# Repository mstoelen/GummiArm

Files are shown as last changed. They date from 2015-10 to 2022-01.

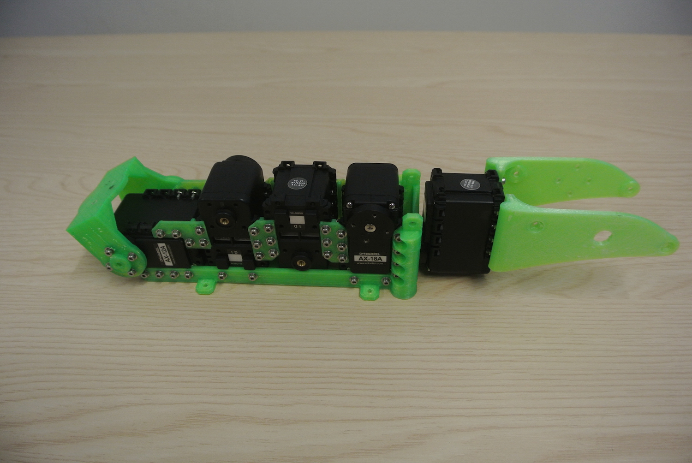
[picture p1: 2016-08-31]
media/instructions/media/building/lower_arm/fourth_step_2.JPG

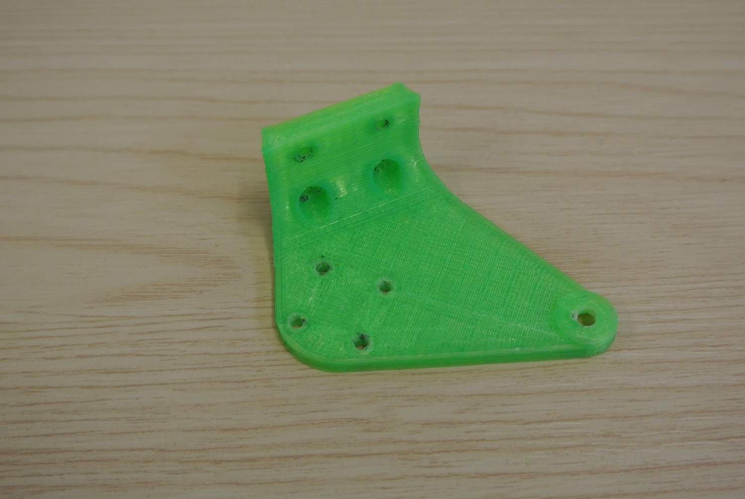
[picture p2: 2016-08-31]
media/instructions/media/plastic/upper_shoulder/left_clavicle.JPG

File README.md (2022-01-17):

# GummiArm

**Note:** This repository was archived on 24/04/2019. Last tested last on ROS Kinetic Kame. Checkout the new GummiArm Community Edition here: https://github.com/GummiArmCE

Repository for the GummiArm robot project: http://mstoelen.github.io/GummiArm/

Documentation in the wiki: https://github.com/mstoelen/GummiArm/wiki

Detailed build instructions <a href="http://htmlpreview.github.io/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">here</a>.

Videos: https://plus.google.com/collection/oGXbV

<br />This work is licensed under a <a rel="license" href="http://creativecommons.org/licenses/by-sa/4.0/">Creative Commons Attribution-ShareAlike 4.0 International License</a>.

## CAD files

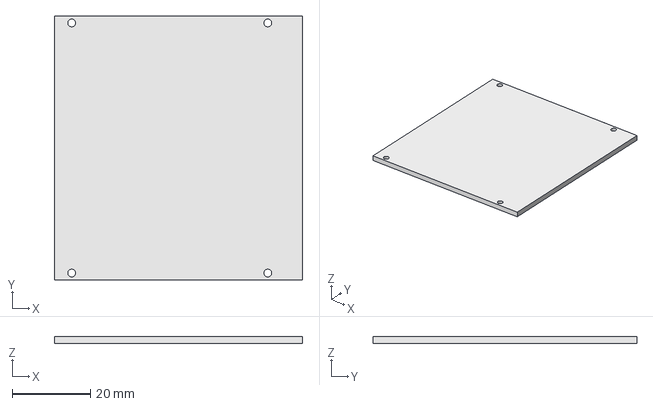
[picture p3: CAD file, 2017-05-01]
printables/accessories/smps_to_dyna_case_top.FCStd
63.6 x 67.6 x 1.86 mm

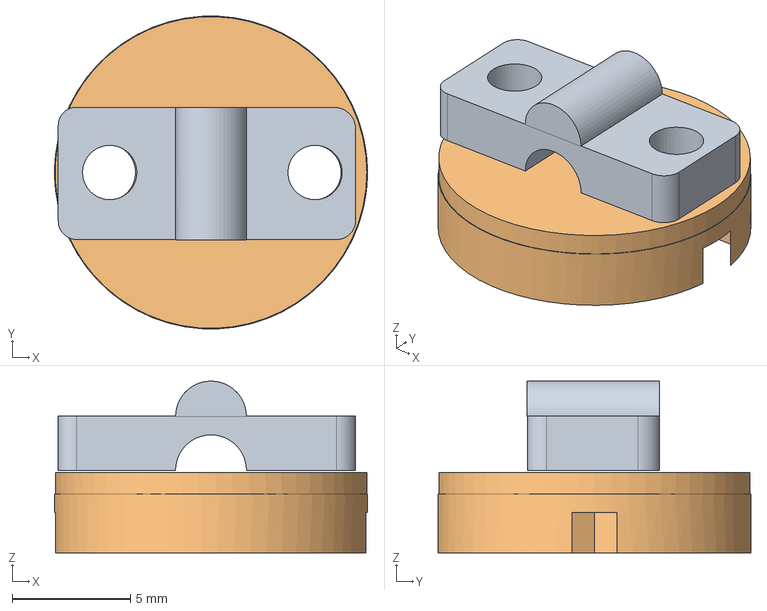
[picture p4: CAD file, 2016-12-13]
printables/common/tendon_joiner.FCStd
13.3 x 13.2 x 7.28 mm
top001

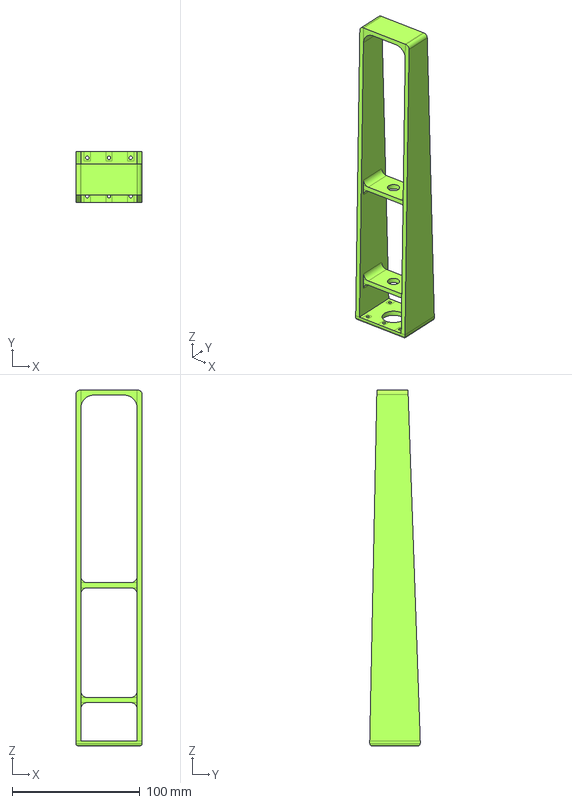
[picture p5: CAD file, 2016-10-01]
printables/dummies/upper_arm_dummy.FCStd
52.0 x 39.6 x 279.0 mm

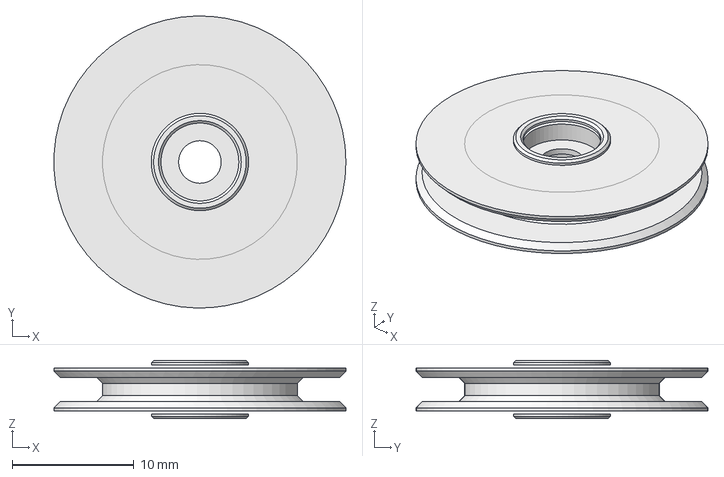
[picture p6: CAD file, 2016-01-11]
printables/hand/big_pulley_w_bearing.FCStd
24.0 x 24.0 x 4.80 mm

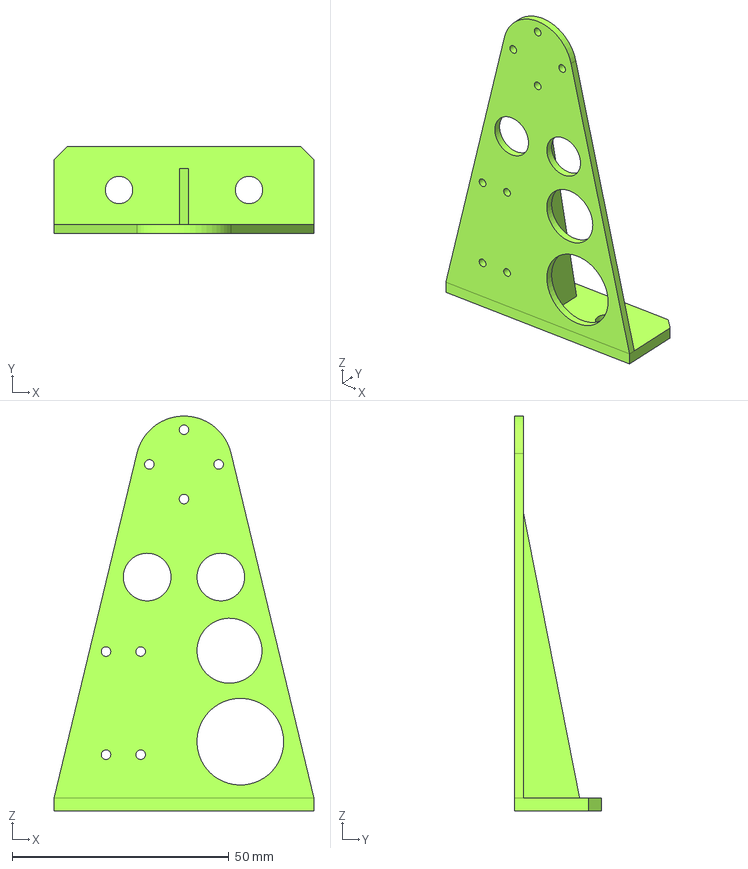
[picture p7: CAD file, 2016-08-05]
printables/head/encoder_frame.FCStd
60.0 x 20.0 x 91.2 mm

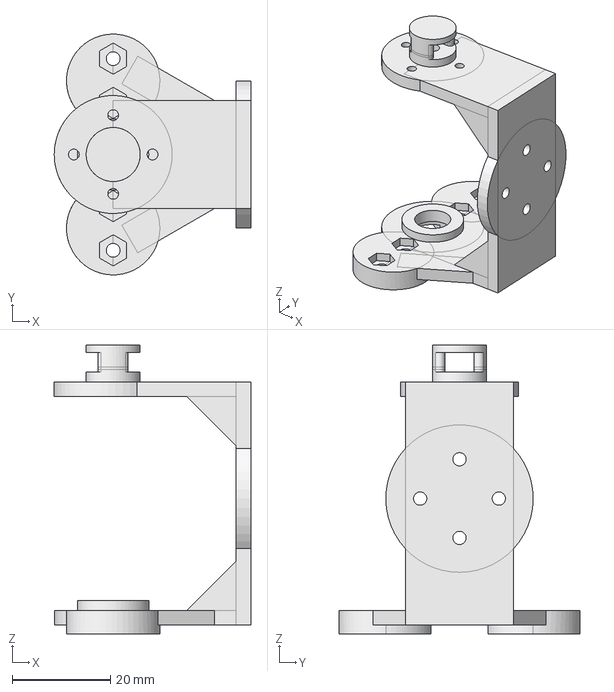
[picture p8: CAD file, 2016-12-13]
printables/lower_arm/wrist_frame.FCStd
40.0 x 49.0 x 58.8 mm

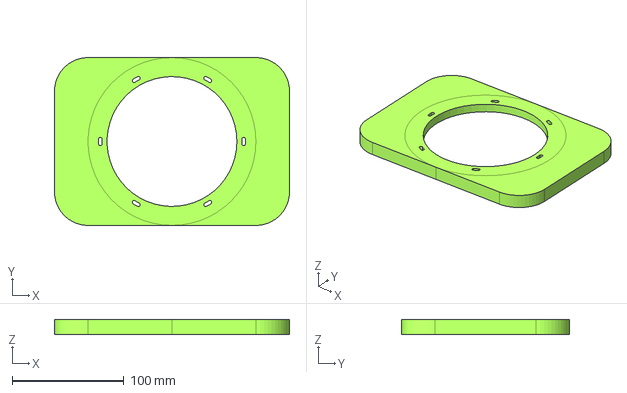
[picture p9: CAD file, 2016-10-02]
printables/mounts/table_flat_mount_bearing.FCStd
210.0 x 150.0 x 13.0 mm

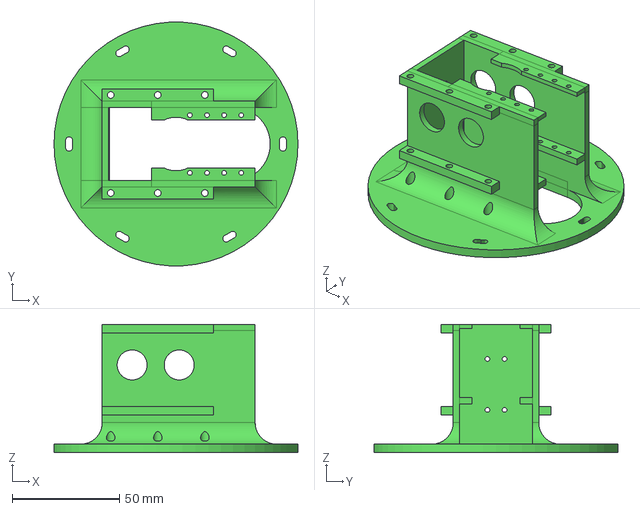
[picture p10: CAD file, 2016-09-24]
printables/shoulder/underside_plate.FCStd
114.0 x 113.8 x 60.0 mm

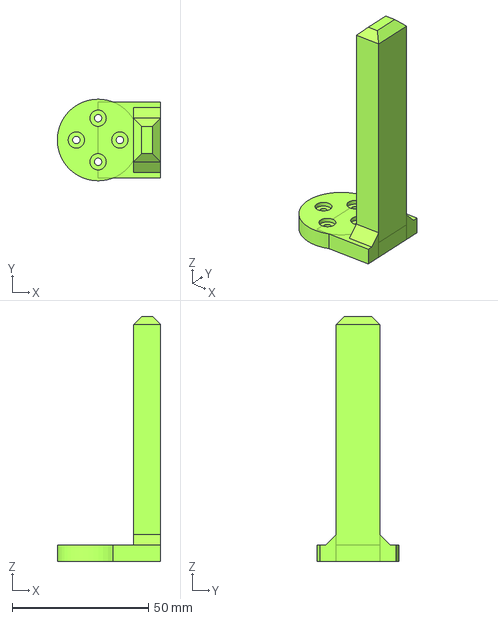
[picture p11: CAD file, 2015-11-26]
printables/tools/straight_finger.FCStd
38.0 x 30.0 x 90.0 mm

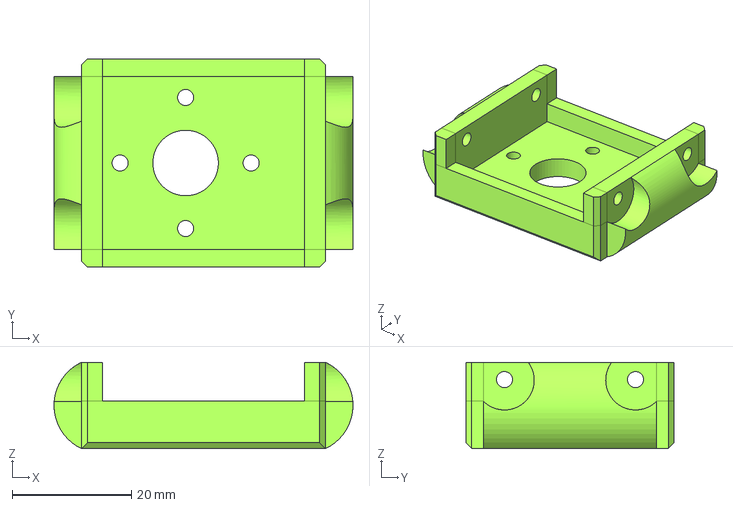
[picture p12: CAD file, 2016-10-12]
printables/upper_arm/top_mx-64_mount.FCStd
50.2 x 35.0 x 14.5 mm

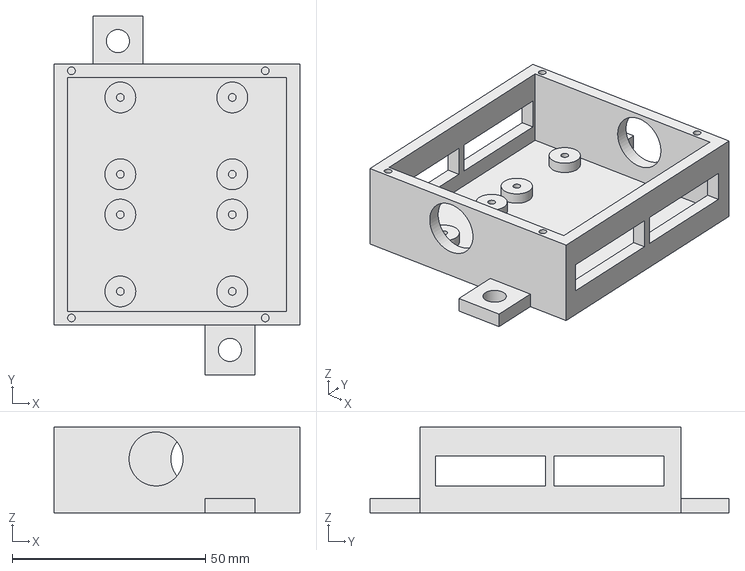
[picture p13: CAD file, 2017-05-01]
printables/accessories/smps_to_dyna_case.FCStd
63.6 x 93.0 x 22.3 mm

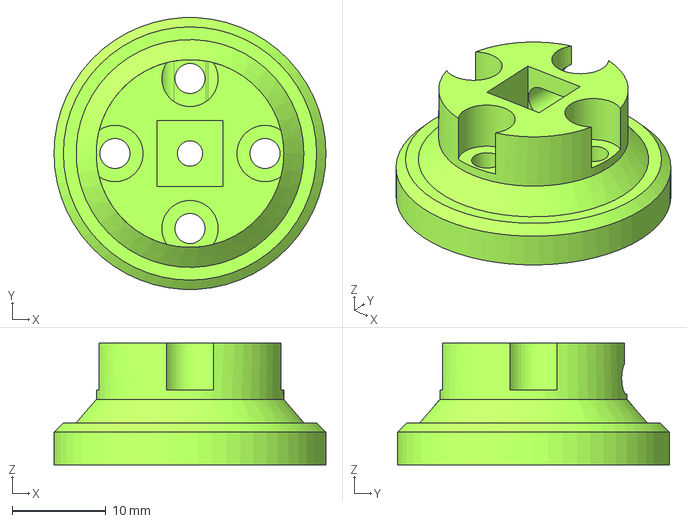
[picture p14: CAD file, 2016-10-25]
printables/common/tendon_wheel_ax_fingers.FCStd
29.0 x 29.0 x 13.0 mm

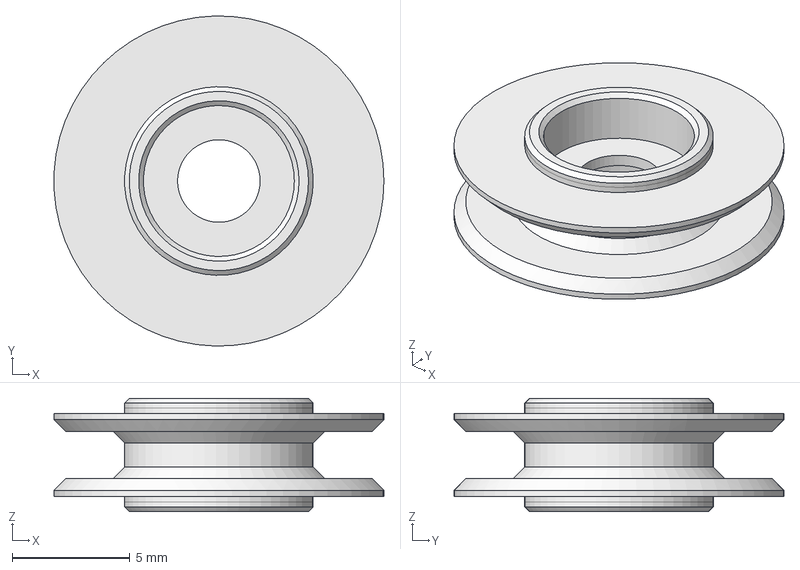
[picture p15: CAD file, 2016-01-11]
printables/hand/small_pulley_w_bearing.FCStd
14.0 x 14.0 x 4.80 mm

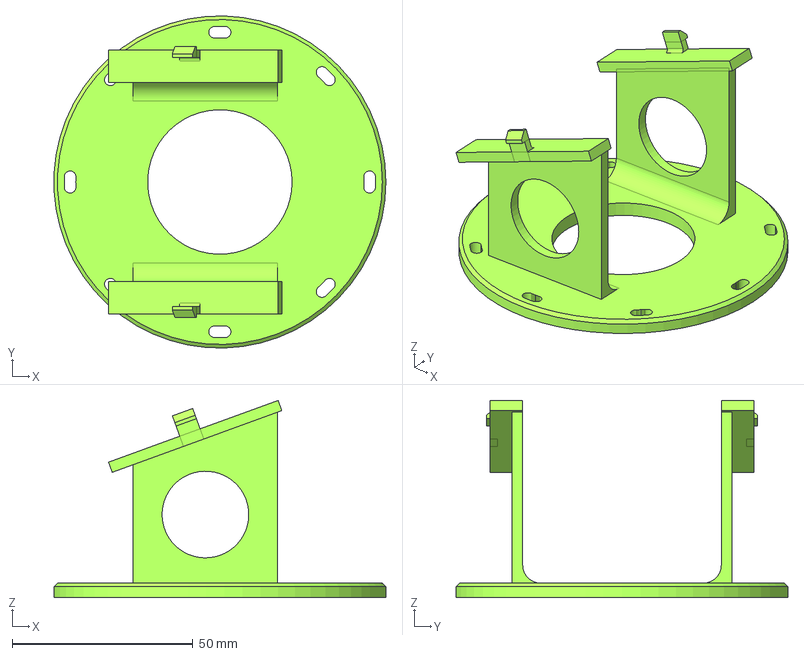
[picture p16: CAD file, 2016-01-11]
printables/head/top_mount.FCStd
91.9 x 92.0 x 54.6 mm

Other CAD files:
printables/lower_arm/arduino_base.stl
printables/mounts/tendon_testbench_strap.FCStd
printables/shoulder/roll_plate.FCStd
printables/tools/just_a_plate.FCStd
printables/accessories/extruded_alu_end.3dm
printables/accessories/smps_to_dyna_case_with_logo.3dm
printables/accessories/smps_to_dyna_case_with_logo.stl
printables/common/line_fastener_for_bolt.FCStd
printables/common/line_fastener_piece.FCStd
printables/common/tendon_fastener_for_bolt_3mm.FCStd
printables/common/tendon_strap.FCStd
printables/common/tendon_wheel_ax_12_15_mm.FCStd
printables/common/tendon_wheel_ax_12_15_mm_top.FCStd
printables/common/tendon_wheel_ax_9_15_mm.FCStd
printables/common/tendon_wheel_ax_9_15_mm_top.FCStd
printables/common/tendon_wheel_ax_9_17_mm.FCStd
printables/common/tendon_wheel_ax_9_17_mm_top.FCStd
printables/common/tendon_wheel_ax_fingers_top.FCStd
printables/common/tendon_wheel_mx_12_23_mm.FCStd
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

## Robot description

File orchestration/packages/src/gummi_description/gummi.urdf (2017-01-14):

<?xml version="1.0" encoding="utf-8"?>

<robot name="gummi">

 <link name="base_link">
    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
  </link>

 <link name="shoulder_preroll">
    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
  </link>

  <link name="shoulder">
    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
    <inertial>
      <origin rpy="0.0 0.0 0.0" xyz="0.0 0.0 0.0"/>
      <mass value="1"/>
      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
    </inertial>
  </link>

  <link name="upperarm_preroll">
    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
    <inertial>
      <origin rpy="0.0 0.0 0.0" xyz="0.0 0.0 0.0"/>
      <mass value="1"/>
      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
    </inertial>
  </link>

  <link name="upperarm">
    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
    <inertial>
      <origin rpy="0.0 0.0 0.0" xyz="0.0 0.0 0.0"/>
      <mass value="1"/>
      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
    </inertial>
  </link>

  <link name="lowerarm_preroll">
    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
    <inertial>
      <origin rpy="0.0 0.0 0.0" xyz="0.0 0.0 0.0"/>
      <mass value="1"/>
      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
    </inertial>
  </link>

  <link name="lowerarm">
    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
    <inertial>
      <origin rpy="0.0 0.0 0.0" xyz="0.0 0.0 0.0"/>
      <mass value="1"/>
      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
    </inertial>
  </link>

  <link name="wrist">
    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
    <inertial>
      <origin rpy="0.0 0.0 0.0" xyz="0.0 0.0 0.0"/>
      <mass value="1"/>
      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
    </inertial>
  </link>

  <link name="coupling">
    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
    <inertial>
      <origin rpy="0.0 0.0 0.0" xyz="0.0 0.0 0.0"/>
      <mass value="1"/>
      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
    </inertial>
  </link>

  <link name="tool">
    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
    <inertial>
      <origin rpy="0.0 0.0 0.0" xyz="0.0 0.0 0.0"/>
      <mass value="1"/>
      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
    </inertial>
  </link>
  
  <joint name="shoulder_yaw" type="revolute">
    <origin rpy="0.0 0.0 0.0" xyz="0.0 0.0 0.0"/>
    <parent link="base_link"/>
    <child link="shoulder_preroll"/>
    <axis xyz="0 0 1"/>
    <limit effort="0" lower="-0.52" upper="1.04" velocity="1.0"/>
  </joint> 
  <joint name="shoulder_roll" type="revolute">
    <origin rpy="1.57079 0.0 0.0" xyz="0.0 0.0 0.107"/>
    <parent link="shoulder_preroll"/>
    <child link="shoulder"/>
    <axis xyz="0 0 1"/>
    <limit effort="0" lower="-0.55" upper="1.4" velocity="1.0"/>
  </joint> 
  <joint name="shoulder_pitch" type="revolute">
    <origin rpy="0 -1.57079 0.0" xyz="0.0 0.0 0.129"/>
    <parent link="shoulder"/>
    <child link="upperarm_preroll"/>
    <axis xyz="0 0 1"/>
    <limit effort="0" lower="-0.15" upper="1.1" velocity="1.0"/>
  </joint>
  <joint name="upperarm_roll" type="revolute">
    <origin rpy="1.57079 0.0 0.0" xyz="0.0 -0.09 0.0"/>
    <parent link="upperarm_preroll"/>
    <child link="upperarm"/>
    <axis xyz="0 0 1"/>
    <limit effort="0" lower="-1.57080" upper="1.57080" velocity="1.0"/>
  </joint>
  <joint name="elbow" type="revolute">
    <origin rpy="0.0 1.57079 0.0" xyz="0.0 -0.0103 0.2035"/>
    <parent link="upperarm"/>
    <child link="lowerarm_preroll"/>
    <axis xyz="0 0 1"/>
    <limit effort="0" lower="-0.85" upper="0.65" velocity="1.0"/>
  </joint>
  <joint name="forearm_roll" type="revolute">
    <origin rpy="1.57079 0.0 0.0" xyz="0.0 -0.079 0.0"/>
    <parent link="lowerarm_preroll"/>
    <child link="lowerarm"/>
    <axis xyz="0 0 1"/>
    <limit effort="0" lower="-2.7489" upper="2.7489" velocity="1.0"/>
  </joint>
  <joint name="wrist_pitch" type="revolute">
    <origin rpy=" 0.0 1.57079 0.0" xyz="0.0 0.0 0.15"/>
    <parent link="lowerarm"/>
    <child link="wrist"/>
    <axis xyz="0 1 0"/>
    <limit effort="0" lower="-0.75" upper="0.75" velocity="1.0"/>
  </joint>
  <joint name="wrist_to_coupling" type="fixed">
    <origin rpy="0.0 0.0 3.14159" xyz="-0.0281 0.0 0.0"/>
    <parent link="wrist"/>
    <child link="coupling"/>
    <axis xyz="0 0 1"/>
    <limit effort="0" lower="-1.57080" upper="1.57080" velocity="1.0"/>
  </joint>
  <joint name="coupling_to_tool" type="fixed">
    <origin rpy="-1.57079 0.0 0.0" xyz="0.075 0.0 0.0"/>
    <parent link="coupling"/>
    <child link="tool"/>
    <axis xyz="0 0 1"/>
    <limit effort="0" lower="-1.57080" upper="1.57080" velocity="1.0"/>
  </joint>
  
</robot>

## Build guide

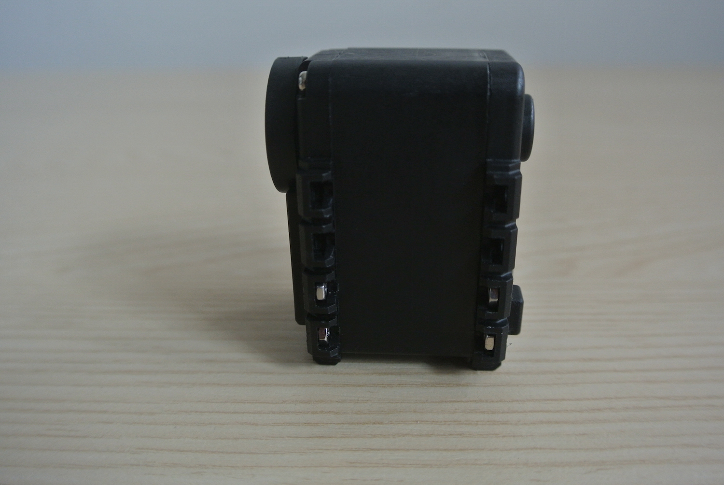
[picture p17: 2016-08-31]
media/instructions/media/servos/s1left.JPG

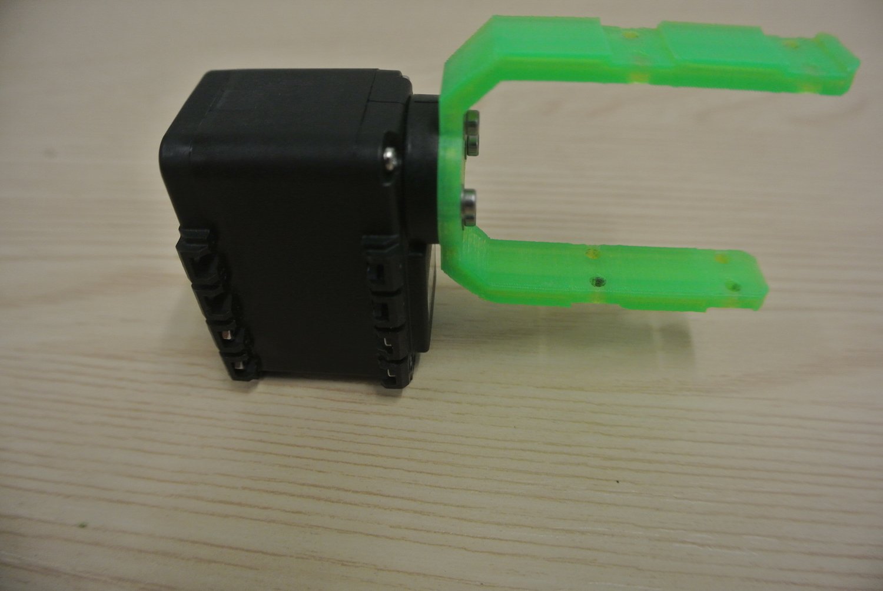
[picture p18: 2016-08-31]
media/instructions/media/building/upper_shoulder/second_step.JPG

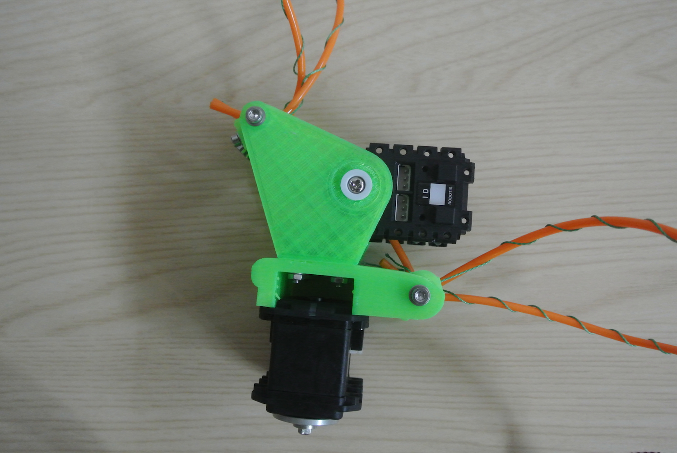
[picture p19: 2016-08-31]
media/instructions/media/building/upper_shoulder/eleventh_step_2.JPG

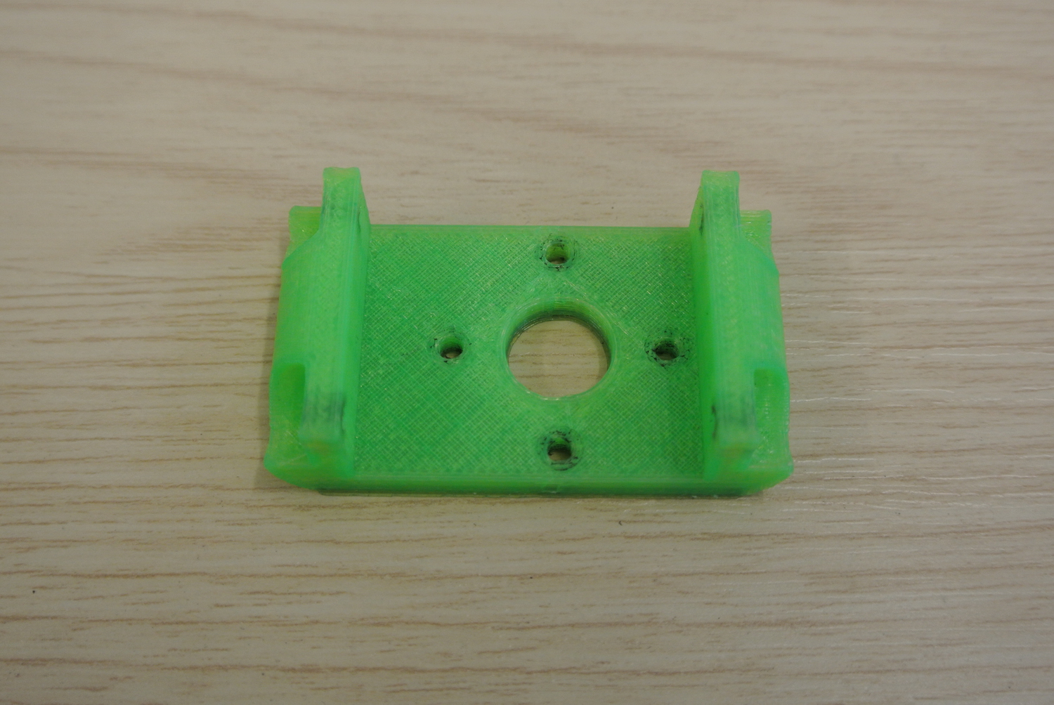
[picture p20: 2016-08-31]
media/instructions/media/plastic/upper_arm/lower_plate.JPG

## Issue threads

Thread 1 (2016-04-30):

Question about building the robot

dgerod, 2016-04-30:
I am interested in the robot and I think that is cool that you share the CAD of the pieces. However, after seeing your videos and looking in this repository I think that more information is needed to build it, for example how to assemble the pieces and how to program the controller. Are you thinking on sharing this information too?

Could I use the robot for personal proposes? My interest is not in building robots but in AI and Robotics and I need something for my personal research in this area.
How many time do you think I will need to build it? And how much it will cost approximately?

Thanks in advance.

mstoelen, 2016-05-02:
Hi, you can certainly use the project for personal (and/or professional) purposes. Please also feel free to contribute!

We are working on a Wiki for documenting the parts needed (beyond the printables), the build process (any help appreciated), the costs associated, and how to install/run the code. For the current 7+1 DOF version (v2.1) the total cost is approaching $5000, mainly due to the beefy MX-106T Dynamixel servos in the shoulder (need an alternative).

Total build time would be great to find out about, not sure. The parts require around 500 grams of PLA in total, likely a week of printing on a typical hobby-grade 3D printer. No soldering is required. Btw, the basic ROS-based controllers are available in the 'orchestration' folder.

Hope this helps, and keep in touch. Happy to support if you decide to build.

dgerod, 2016-05-04:
Thanks for your answer!

The price should not be a problem so I am still interested on it :-).

However, I have an important question, are you using it to do Learning by Demonstration?
In my research work I have to teach the robot by hand to pick objects, do you think that your robot is feasible for doing this task? The trajectories will be executed in joint space and not in Cartesian space.

mstoelen, 2016-05-09:
Hi, yes that type of learning is one potential application. Right now you can teleoperate the arm (we use a £100 space navigator joystick), and record joint angles or Cartesian pose. Also working on kinesthetic teaching, through force sensing in joints, but still work in progress.

dgerod, 2016-05-11:
Good to know, I am really interesting on the kinesthetic teaching as it is one of my essential requirements for the robot.

When you have the wiki ready, or a preliminary version, I will take a look to understand better what is needed to build the robot. Please, let me know when it is ready, thanks.

mstoelen, 2016-05-20:
A preliminary version of the wiki is now up, check it out here: https://github.com/mstoelen/GummiArm/wiki

mstoelen, 2016-09-06:
Hi, just to let you know that we are working on detailed build instructions right now. See progress [here](http://htmlpreview.github.com/?https://github.com/mstoelen/GummiArm/blob/master/media/instructions/build.html)

dgerod, 2016-09-07:
Thanks for sharing!
I would like to follow the process... but the link is not working ;-)

mstoelen, 2016-09-07:
Strange, it opens fine in my browser (Safari). What browser are you using?
You can also clone the repository, then open this html locally on your computer: [https://github.com/mstoelen/GummiArm/blob/master/media/instructions/build.htm](https://github.com/mstoelen/GummiArm/blob/master/media/instructions/build.htm)

dgerod, 2016-09-07:
I use Firefox but it was a problem in the configuration of my browser, sorry. I should had tried another browser (i.e. Chrome) to check the link.

I will study the process during the week end as I would like to understand it well. However, I have just done a quick check and it seems very good. Thanks again for sharing.

Closed 2016-09-30.

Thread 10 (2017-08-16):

Remove equilibrium sign parameter

mstoelen, 2017-08-16:
Wrong in ghost for shoulder pitch and elbow.

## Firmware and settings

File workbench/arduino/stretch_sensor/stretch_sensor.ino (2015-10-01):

#include "RunningAverage.h" /* http://playground.arduino.cc/Main/RunningAverage */
#include <Servo.h>

int sensor_pin = A0;
int size_running = 50;

int sensor_value = 0; 
int servo_value = 0;
float average = 0.0;
int counter = 0;

Servo my_servo;
RunningAverage running(size_running);

void setup() {
  my_servo.attach(13);
  Serial.begin(9600);
  running.fillValue(0.0, size_running);
}

void loop() {
  sensor_value = analogRead(sensor_pin); 
  
  servo_value = map(sensor_value, 970, 990, 0, 179);
  running.addValue(servo_value);
  average = running.getAverage();
  
  if ((average >= 0) && (average <= 255)) {
    my_servo.write(average);
    
    if(counter > 20) {
      Serial.print("Input: ");
      Serial.print(sensor_value);
      Serial.print(", servo output (averaged): ");
      Serial.print(average);
      Serial.print(".");
      Serial.println();
      counter = 0;
    }
  }
  else {
    Serial.println("Outside range.");
  } 
  
  counter++;
  delay(5);  
}

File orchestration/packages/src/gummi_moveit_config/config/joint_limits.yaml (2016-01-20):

# joint_limits.yaml allows the dynamics properties specified in the URDF to be overwritten or augmented as needed
# Specific joint properties can be changed with the keys [max_position, min_position, max_velocity, max_acceleration]
# Joint limits can be turned off with [has_velocity_limits, has_acceleration_limits]
joint_limits:
  elbow:
    has_velocity_limits: true
    max_velocity: 1
    has_acceleration_limits: false
    max_acceleration: 0
  forearm_roll:
    has_velocity_limits: true
    max_velocity: 1
    has_acceleration_limits: false
    max_acceleration: 0
  shoulder_pitch:
    has_velocity_limits: true
    max_velocity: 1
    has_acceleration_limits: false
    max_acceleration: 0
  shoulder_roll:
    has_velocity_limits: true
    max_velocity: 1
    has_acceleration_limits: false
    max_acceleration: 0
  shoulder_yaw:
    has_velocity_limits: true
    max_velocity: 1
    has_acceleration_limits: false
    max_acceleration: 0
  upperarm_roll:
    has_velocity_limits: true
    max_velocity: 1
    has_acceleration_limits: false
    max_acceleration: 0
  wrist_pitch:
    has_velocity_limits: true
    max_velocity: 1
    has_acceleration_limits: false
    max_acceleration: 0

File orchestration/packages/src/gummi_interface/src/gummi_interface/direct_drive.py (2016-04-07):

#!/usr/bin/env python

import rospy

from std_msgs.msg import Float64

from joint_angle import JointAngle
from dynamixel_controllers.srv import SetTorqueLimit

class DirectDrive:
    def __init__(self, name, servoRange):
        self.name = name
        self.servoRange = servoRange
        self.initPublishers()
        self.initVariables()

        self.angle = JointAngle(name, 1, -servoRange/2, servoRange/2, False)

    def initPublishers(self):
        self.pub = rospy.Publisher(self.name + '_controller/command', Float64, queue_size=5)

    def initVariables(self):
        self.velocity = False
        self.noCommandYet = True

    def servoTo(self, dAngle):
        self.velocity = False
        self.angle.setDesired(dAngle)
        self.noCommandYet = False
        self.doUpdate()

    def servoWith(self, dVelocity):
        self.velocity = True
        self.angle.setDesiredVelocity(dVelocity)
        self.noCommandYet = False
        self.doUpdate()

    def publishCommand(self):
        dAngle = self.angle.getDesired()
        self.pub.publish(dAngle)

    def doUpdate(self):
        if self.velocity:
            self.angle.doVelocityIncrement()
            
        if self.noCommandYet:
            self.angle.setDesired(self.encoderAngle)
            
        self.publishCommand()

    def getJointAngle(self):
        return self.angle.getEncoder()

    def setTorqueLimit(self, limit):
        service_name = self.name + "_controller/set_torque_limit"
        rospy.wait_for_service(service_name)
        try:
            te = rospy.ServiceProxy(service_name, SetTorqueLimit)
            te(limit)
        except rospy.ServiceException, e:
            print "Service call failed: %s"%e

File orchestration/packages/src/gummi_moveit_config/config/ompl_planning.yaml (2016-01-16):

planner_configs:
  SBLkConfigDefault:
    type: geometric::SBL
    range: 0.0  # Max motion added to tree. ==> maxDistance_ default: 0.0, if 0.0, set on setup()
  ESTkConfigDefault:
    type: geometric::EST
    range: 0.0  # Max motion added to tree. ==> maxDistance_ default: 0.0, if 0.0 setup()
    goal_bias: 0.05  # When close to goal select goal, with this probability. default: 0.05
  LBKPIECEkConfigDefault:
    type: geometric::LBKPIECE
    range: 0.0  # Max motion added to tree. ==> maxDistance_ default: 0.0, if 0.0, set on setup()
    border_fraction: 0.9  # Fraction of time focused on boarder default: 0.9
    min_valid_path_fraction: 0.5  # Accept partially valid moves above fraction. default: 0.5
  BKPIECEkConfigDefault:
    type: geometric::BKPIECE
    range: 0.0  # Max motion added to tree. ==> maxDistance_ default: 0.0, if 0.0, set on setup()
    border_fraction: 0.9  # Fraction of time focused on boarder default: 0.9
    failed_expansion_score_factor: 0.5  # When extending motion fails, scale score by factor. default: 0.5
    min_valid_path_fraction: 0.5  # Accept partially valid moves above fraction. default: 0.5
  KPIECEkConfigDefault:
    type: geometric::KPIECE
    range: 0.0  # Max motion added to tree. ==> maxDistance_ default: 0.0, if 0.0, set on setup()
    goal_bias: 0.05  # When close to goal select goal, with this probability. default: 0.05 
    border_fraction: 0.9  # Fraction of time focused on boarder default: 0.9 (0.0,1.]
    failed_expansion_score_factor: 0.5  # When extending motion fails, scale score by factor. default: 0.5
    min_valid_path_fraction: 0.5  # Accept partially valid moves above fraction. default: 0.5
  RRTkConfigDefault:
    type: geometric::RRT
    range: 0.0  # Max motion added to tree. ==> maxDistance_ default: 0.0, if 0.0, set on setup()
    goal_bias: 0.05  # When close to goal select goal, with this probability? default: 0.05
  RRTConnectkConfigDefault:
    type: geometric::RRTConnect
    range: 0.0  # Max motion added to tree. ==> maxDistance_ default: 0.0, if 0.0, set on setup()
  RRTstarkConfigDefault:
    type: geometric::RRTstar
    range: 0.0  # Max motion added to tree. ==> maxDistance_ default: 0.0, if 0.0, set on setup()
    goal_bias: 0.05  # When close to goal select goal, with this probability? default: 0.05
    delay_collision_checking: 1  # Stop collision checking as soon as C-free parent found. default 1
  TRRTkConfigDefault:
    type: geometric::TRRT
    range: 0.0  # Max motion added to tree. ==> maxDistance_ default: 0.0, if 0.0, set on setup()
    goal_bias: 0.05  # When close to goal select goal, with this probability? default: 0.05
    max_states_failed: 10  # when to start increasing temp. default: 10
    temp_change_factor: 2.0  # how much to increase or decrease temp. default: 2.0
    min_temperature: 10e-10  # lower limit of temp change. default: 10e-10
    init_temperature: 10e-6  # initial temperature. default: 10e-6
    frountier_threshold: 0.0  # dist new state to nearest neighbor to disqualify as frontier. default: 0.0 set in setup() 
    frountierNodeRatio: 0.1  # 1/10, or 1 nonfrontier for every 10 frontier. default: 0.1
    k_constant: 0.0  # value used to normalize expresssion. default: 0.0 set in setup()
  PRMkConfigDefault:
    type: geometric::PRM
    max_nearest_neighbors: 10  # use k nearest neighbors. default: 10
  PRMstarkConfigDefault:
    type: geometric::PRMstar
right_arm:
  planner_configs:
    - SBLkConfigDefault
    - ESTkConfigDefault
    - LBKPIECEkConfigDefault
    - BKPIECEkConfigDefault
    - KPIECEkConfigDefault
    - RRTkConfigDefault
    - RRTConnectkConfigDefault
    - RRTstarkConfigDefault
    - TRRTkConfigDefault
    - PRMkConfigDefault
    - PRMstarkConfigDefault
  projection_evaluator: joints(shoulder_yaw,shoulder_roll)
  longest_valid_segment_fraction: 0.05

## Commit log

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2015-05-31 Completed first iteration of lower arm.
    [elbow_frame_mirrored.FCStd, elbow_roll_frame_4_servo.FCStd, inter_mx-18_fastener.FCStd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]
2015-05-31 Name changes to stick to a convention.
    [tendon_wheel_ax-18_3_mm.FCStd, tendon_wheel_ax-18_top_3_mm.FCStd, tendon_wheel_mx-64_3_mm_side.FCStd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]
2015-06-18 Bringing repo up-to-date as of early June videos.
    [cup.FCStd, elbow_roll_frame_4_servo.FCStd, table_mount_bottom.FCStd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]
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2015-09-22 Reinforced mx-64 mount.
    [top_mx-64_mount_to_mx-28.FCStd]
2015-09-22 Bringing shoulder and tools up to date.
    [back_plate_shoulder.FCStd, back_roll_plate.FCStd, bottom_plate.FCStd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]
2015-09-22 Latest and renamed tendond wheels.
    [tendon_wheel_ax_12_15_mm.FCStd, tendon_wheel_ax_12_15_mm_top.FCStd, tendon_wheel_mx-64_3_mm_side.FCStd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]
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2015-09-26 ROS packages for basic teleoperation.
    [fake_controllers.yaml, gummi.urdf, joint_limits.yaml]
2015-09-26 FreeCAD macro script for generating .stl files.
    [roll_plate.FCStd]
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2015-10-11 Smaller radius AX-18 pulleys.
    [tendon_wheel_ax_9_15_mm.FCStd, tendon_wheel_ax_9_15_mm_top.FCStd]
2015-10-19 Adjusting everything. Still issues with interference on overload of Ax-18s.
    [gummi.urdf]
2015-10-22 Discovered spikes in MX-12 encoder readings - median fix, for now.
    [antagonist.py, joint_angle.py]
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2015-10-25 Ready for interaction test.
    [gummi.urdf]
2015-10-26 New HW integrated, and split power into 3 sections.
    [back_plate_shoulder.FCStd, encoder_plate.FCStd, frame_rigid_mount.FCStd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]
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2015-11-22 First model files for head.
    [bottom_mount.FCStd, top_mount.FCStd, underside_plate.FCStd]
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2015-12-09 Slightly better handling of encoder noise.
    [joint_angle.py]
2015-12-10 Trying to iron out networking issues, more todo.
    [antagonist.py, direct_drive.py, joint_angle.py]
2015-12-21 Small pulley for hand.
    [small_pulley_w_bearing.FCStd, top_mount.FCStd]
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2016-01-16 Not yet working, but ok in rviz.
    [fake_controllers.yaml, gummi.urdf, joint_limits.yaml]
2016-01-16 Working 7DOF teleop, should now try weighting joints.
    [gummi.urdf]
2016-01-17 Tried including in teleop node, but missing check for joint angles, likely not the way either.
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2016-01-20 Found differences in naming of joints (todo: central), now ok pose control.
    [fake_controllers.yaml, gummi.urdf, joint_limits.yaml]
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2016-02-20 Skin mounting points for elbow roll frame.
    Former-commit-id: 9bef118e79a0bf5f9bdf6f7e6a534702fe0cd6d1
    [elbow_roll_frame_4_servo.FCStd]
2016-02-20 Reducing max angle of shoulder pitch, for now.
    Former-commit-id: 51ec02b0c78f1b95fd418b547ff2ecc14c992b4e
    [gummi.urdf]
2016-02-27 From stiffness to cocontraction (naming) in interface.
    Former-commit-id: a682a9c7bd5d02de0f539eeffd2badec66797164
    [antagonist.py, gummi.py]
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2016-02-28 Calibration as ROS parameters.
    Former-commit-id: a26cfe7a8fb27db07ec5dd7f1c1f9cc0057f87e8
    [calibration_elbow.yaml, calibration_shoulder_pitch.yaml, calibration_shoulder_roll.yaml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]
2016-02-28 Agonist to flexor etc.
    Former-commit-id: c6c6ee1d91deea4a59c9716bc35ce02d4e7ad1db
    [calibration_elbow.yaml, calibration_shoulder_pitch.yaml, calibration_shoulder_roll.yaml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]
2016-02-28 Moving to COSMOS.
    Former-commit-id: 9c27f4ec1bca9e021cb3fde379445cd1e93f1abe
    [calibration_shoulder_pitch.yaml, calibration_shoulder_roll.yaml, calibration_shoulder_yaw.yaml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]
2016-02-28 Working script for saving calibration to yaml file.
    Former-commit-id: 3b67943c8b9b4a2cfcd8737f9015af10062afe78
    [calibration_elbow.yaml]
2016-02-29 First full calibration file for elbow.
    Former-commit-id: 3b08187809d4bbe48024f61becdbbd338a613375
    [calibration_elbow.yaml]
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2016-02-29 Getting closer.
    Former-commit-id: 85d11790028aeb30c65f7f0770f7b4e0273cfd03
    [calibration_elbow.yaml]
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2016-03-01 Using full elbow range.
    Former-commit-id: 006f8675377576dc44a0a4f4f0b6a69d6c9c37b5
    [gummi.urdf]
2016-03-01 Calibrated elbow and shoulder yaw.
    Former-commit-id: 53f387d65e36b0dd6cf316ee6f00d9ae58b1f581
    [calibration_elbow.yaml, calibration_shoulder_yaw.yaml]
2016-03-02 Better calibration (full range), now of full arm.
    Former-commit-id: 9a31192def98458b2506cac7405faf2a6e310f39
    [calibration_elbow.yaml, calibration_shoulder_pitch.yaml, calibration_shoulder_roll.yaml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]
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2016-03-09 Lower arm rotated 90 degrees inwards.
    Former-commit-id: bb80be88d40fab6b68fe0df4a31f74296afaf685
    [gummi.urdf]
2016-03-14 Almost ready for tests.
    Former-commit-id: 05dfd26c2b266ffa6b97c9bc9c2b4404aa67f2c0
    [calibration_elbow.yaml]
2016-03-15 Reduced pull on wrist to avoid overheating.
    Former-commit-id: 688263f08462cd5b6ca8de98d9b2373138890c05
    [calibration_wrist.yaml, gummi.urdf]
2016-03-16 Fixed error in script.
    Former-commit-id: df54f7259a30fb2eab37a0fb94231971de4530c0
    [antagonist.py, gummi.py, reflex.py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]
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2016-03-17 Elbow calibrated with forearm at 0.
    Former-commit-id: 761b0179f28e0db075ff726549e25f97057bc8fd
    [calibration_elbow.yaml]
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2016-03-17 Wrist calibrated at 0 degrees.
    Former-commit-id: fec0c5ce6820e5a5e0773c7632b1453aa4c7d207
    [calibration_wrist.yaml]
2016-03-23 Better URDF, 15 deg condition for cocontraction, and full arm test ok.
    Former-commit-id: ad5dc139e12b09d9358f66f81361f8bac21b30ed
    [gummi.urdf]
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2016-04-01 Overheating in biceps with 40 Hz?
    Former-commit-id: 234bd736cbb3881e6c8900be452224a2e165c8b9
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2016-04-01 Updated full-range elbow calibration.
    Former-commit-id: 1f3c0c09ad67d4c7e758ec88dae550f8f02f37e0
    [calibration_elbow.yaml]
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2016-04-07 Little fixes.
    Former-commit-id: ace31487b580676e4443f2fea3869d9bf57a7067
    [gummi.py, wrist.yaml]
2016-04-07 Teleop range corrected.
    Former-commit-id: 99e4d4087be7b58c68afabae25300d718434098a
    [equilibrium_model.py]
2016-04-11 Primitive collision reflex with forwards model.
    Former-commit-id: deffb160ea8d3f9d9ac6689072fade79ab7d4263
    [antagonist.py, elbow.yaml, reflex.py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]
2016-04-12 Basic active collision compliance, also during teleop.
    Former-commit-id: 09cd093dd2ca7230c483ae1a10d822fdf9303e70
    [antagonist.py]
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2016-04-12 Need to go over mapping for forward models.
    Former-commit-id: 2b90ad457dbf5ade102995b9c92a7aea94f12b7b
    [calibration_shoulder_pitch.yaml, calibration_wrist.yaml, gummi.urdf]
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2016-04-14 reinforced.
    Former-commit-id: aeab00e7cf34284704905f430c816d780577ad11
    [top_mx-64_mount_to_mx-28.FCStd]
2016-07-29 Missing shoulder parts.
    Former-commit-id: c5e24d6e3a97f2c8e0e6ce52aefa60f2e030356f
    [encoder_frame.FCStd, hub_plate.FCStd, two_tendon_strap.FCStd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]
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2016-08-10 Testbench for tendon testing with MX-64.
    Former-commit-id: 91c7664e66099aff72bf263fab76690a1ec73850
    [tendon_testbench.FCStd, tendon_testbench_strap.FCStd]
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2016-10-12 Missing piece for upper arm.
    [top_mx-64_mount.FCStd]
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2017-01-18 Safety feature, must manually specify clone, or copy files to default folder.
    [calibration_elbow.yaml, calibration_shoulder_pitch.yaml, calibration_shoulder_roll.yaml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]
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2017-05-03 Resolved conflicts.
    [arduino_base.3dm, arduino_base.stl, back_plate_shoulder.FCStd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]
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2017-05-03 Revert "Finalized changes to moveit branch."
    This reverts commit e0085dd01f767fc14ee5c66352b248a750c5e6e5, reversing
    changes made to f92411ed7ddb5d8e8e6bc52a110b9c2c41ccf624.
    [arduino_base.3dm, arduino_base.stl, back_plate_shoulder.FCStd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]
2017-05-03 Revert "Tried to re-add printables in FreeCAD format."
    This reverts commit 5d6dcc1ef3a87f8d3e4ae0e953d6971713e2eaf6.
    [arduino_base.3dm, back_plate_shoulder.FCStd, back_roll_plate.FCStd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]
2017-05-03 Revert "Resolved conflicts."
    This reverts commit a91114f320a3163b1ac2b17d900dac2e9b27a141.
    [arduino_base.3dm, back_plate_shoulder.FCStd, back_roll_plate.FCStd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]
2017-06-02 Missing dyna case
    [smps_to_dyna_case.FCStd, smps_to_dyna_case_top.FCStd]
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2017-12-16 Correct horizontal adduction/abduction according to build instruction servo IDs.
